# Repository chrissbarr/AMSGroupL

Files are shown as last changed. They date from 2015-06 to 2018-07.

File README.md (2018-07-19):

# Aim
The aim of our project is to design a robot that will demonstrate capabilities useful for search and rescue and emergency response operations. Our intended design will be capable of navigating and mapping a largely unknown environment, detecting and localising sound-emitting objects or persons, and determining a person’s status based on observed body temperature, detected sounds (as of breathing, talking, cries for help) and any observed motion using the on-board camera.

This capability could then be used either to notify on-site responders to the presence and locations of potential rescue candidates, or possibly even to provide some form of immediate assistance or medical treatment – however, that is outside of the bounds of this project, and is simply an example of the real-world applications of the system. For the purposes of this project, the system will sound an audible alert if a potential survivor is detected.

# Required Hardware
Our system will use a LIDAR unit for localisation and environmental mapping (SLAM), an IR temperature sensor to measure object temperatures in order to differentiate between debris and living people, and an array of microphones in order to perform sound localization. 

# Needs
* Ability to simultaneously localise within and map a bounded, but largely unknown environment
* Ability to navigate the environment based on the internally generated map
*	Ability to locate potential survivors based on sound
*	Ability to determine if a potential survivor is living or not
*	Ability to alert others to presence of survivor

# Requirements
## Core Requirements
*	Able to map the immediate environment as an occupancy grid that correlates with 85% to the ideal occupancy grid.
*	Able to accurately measure temperature of nearby objects (< 50cm, in front of IR temp sensor) within +/- 2°C.
*	Able to choose the most efficient pathway through the mapped environment > 90% of the time.
*	Able to localise multiple impulse sound sources within a 10m radius to within +/- 50cm accuracy, in robot-centric coordinates (as in finding preplaced sonic beacons). In a multi-robot scenario, such beacons will notionally have been placed by a previous "pathfinder" robot, which we will simulate by manual placement of beacons.
*	Able to traverse the perimeter of a detected object (e.g. Lumelski-class algorithms) while maintaining a fixed distance from the perimeter within +/- 5%.
*	Able to determine (with 75% accuracy) whether or not the object of interest is a living person.

## Extension Requirements
*	Able to successfully image the object of interest with 75% certainty that the correct object is the subject.
*	Able to detect the motion of nearby objects in front of the platform (for objects > 10cm moving at > 0.1 m/s). This is simply detecting whether or not there is motion, not the properties of that motion.
*	Capable of selecting station points around an object of interest (ranging from the size of the robot to the size of a prone person) for the purposes of achieving efficient imaging coverage (with overlap between successive images of 10% +/- TBD) at a distance from the object dependent on the given cameras FOV.

# Test Method
The proposed system will be required to navigate a test space consisting of unknown stationary obstacles, sporadic-sound sources both at temperatures in the defined human body-temperature range (simulated by an actual person), and at other temperatures outside this range (simulated by a radio or similar sound emitting object). 

The system will be evaluated on how accurately it can localise a sound source, how successfully it can navigate the unknown environment towards that sound source, and how effective its ability to differentiate between survivor candidates and other sound sources.

# Group Members
*	Chris Barr
    * SLAM
    * IR Temp
*	Bobby Nansel
    *	Sound Detection and Localisation
*	Eric Lai
    *	Close-Range Object Avoidance
    *	Dead Reckoning (Motor Encoders + IMU)
*	Premkumar Katti
    *	Navigation
    *	Path Planning

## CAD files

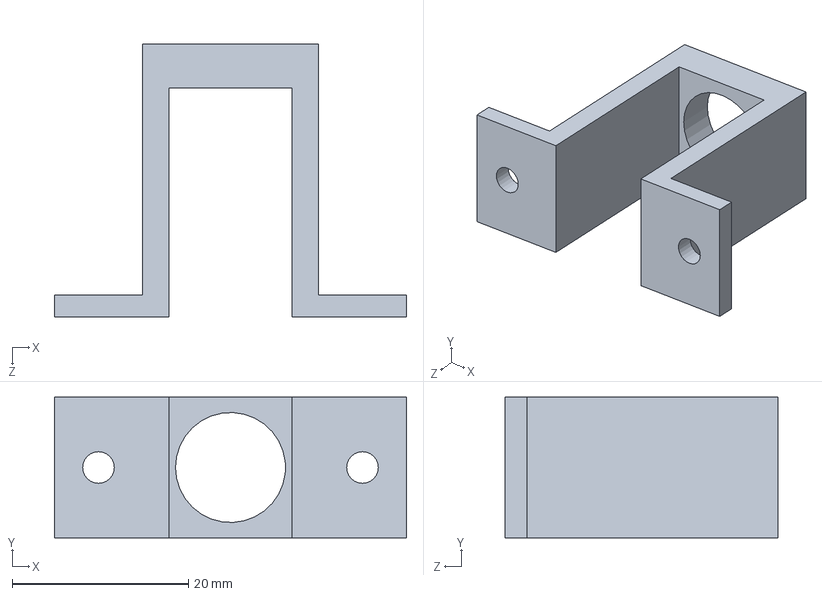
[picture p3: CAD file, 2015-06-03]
IRTempBracket/bracket1.SLDPRT
40.0 x 16.0 x 31.0 mm

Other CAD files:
IRTempBracket/bracket1_2.STL
IRTempBracket/bracket1.STL

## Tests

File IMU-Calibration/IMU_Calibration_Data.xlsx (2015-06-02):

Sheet: Calibration
Accelerometer Calibration |  |  |  | Gyroscope Calibration |  | Magnetometer Calibration
Orientation | X | Y | Z | Noise Upper Limit | 18 |  | X | Y | Z
0 | -0.12 | -5.73 | 238.91 | Minimum Angular Velocity | 40.00 | Min | -527.37 | -705.77 | -552.12
1 | 0.00 | -3.67 | -283.95 | Yaw (Table Edge) | 0.00 | Max | 547.05 | 503.17 | 472.97
2 | -46.75 | -268.88 | -25.88 | Yaw (1/2 rotation) | 179000.00
3 | 45.79 | 259.43 | -22.79 | Difference: | 179000 | Scale | 537.21 | 604.47 | 512.55
4 | -263.80 | 41.00 | -25.80 | Gyro Scale | -56977.46963 | Offset | 9.84 | -101.30 | -39.58
5 | 262.50 | -52.12 | -21.75
Scale: | 263.15 | 264.15 | 261.43
Offset: | -0.65 | -4.72 | -22.52

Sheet: 0
0 | -6 | 239
0 | -6 | 238
0 | -6 | 239
0 | -6 | 239
-1 | -5 | 239
0 | -5 | 239
0 | -5 | 239
0 | -6 | 239
0 | -6 | 239
0 | -5 | 239
0 | -6 | 239
0 | -6 | 239
0 | -6 | 239
0 | -5 | 239
0 | -5 | 239
0 | -6 | 239
0 | -6 | 239
-1 | -6 | 239
0 | -6 | 239
0 | -6 | 239
0 | -6 | 239
0 | -6 | 239
-1 | -5 | 238
0 | -6 | 239
0 | -6 | 238
0 | -6 | 239
0 | -6 | 239
-1 | -6 | 239
0 | -6 | 239
0 | -6 | 239
0 | -5 | 239
0 | -6 | 239
0 | -5 | 239
-0.1212121212 | -5.727272727 | 238.9090909
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

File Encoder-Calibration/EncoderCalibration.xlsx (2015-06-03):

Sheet: Calculations
 |  |  |  |  |  | Encoder Data
 | Vicon Reference Data (m) |  |  |  |  | Left Encoder |  |  | Right Encoder |  |  | Average
 | Start X | Start Y | End X | End Y | Distance Travelled | Start | End | Difference | Start | End | Difference |  | mm / tick
Trial 1 | 3.38 | 2.55 | 4.57 | 2.48 | 1.19 | 50251 | 75407 | 25156 | 50293 | 75496 | 25203 | 25179.5 | 0.0474
Trial 2 | 5.75 | 2.43 | 6.94 | 2.40 | 1.18 | 100464 | 125510 | 25046 | 100606 | 125701 | 25095 | 25070.5 | 0.0472
Trial 3 | 6.89 | 2.33 | 5.70 | 2.44 | 1.19 | 125509 | 150677 | 25168 | 125701 | 150905 | 25204 | 25186 | 0.0472
Trial 4 | 5.70 | 2.44 | 4.51 | 2.55 | 1.19 | 150677 | 175840 | 25163 | 150905 | 176109 | 25204 | 25183.5 | 0.0474
Average |  |  |  |  | 1.19 |  |  | 25133.25 |  |  | 25176.5 | 25154.875 | 0.0473
Angular: | Actual | Calculated | Diff | %
 | 18.24955592 | 18.80355592 | 0.554 | 97.05374876%
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

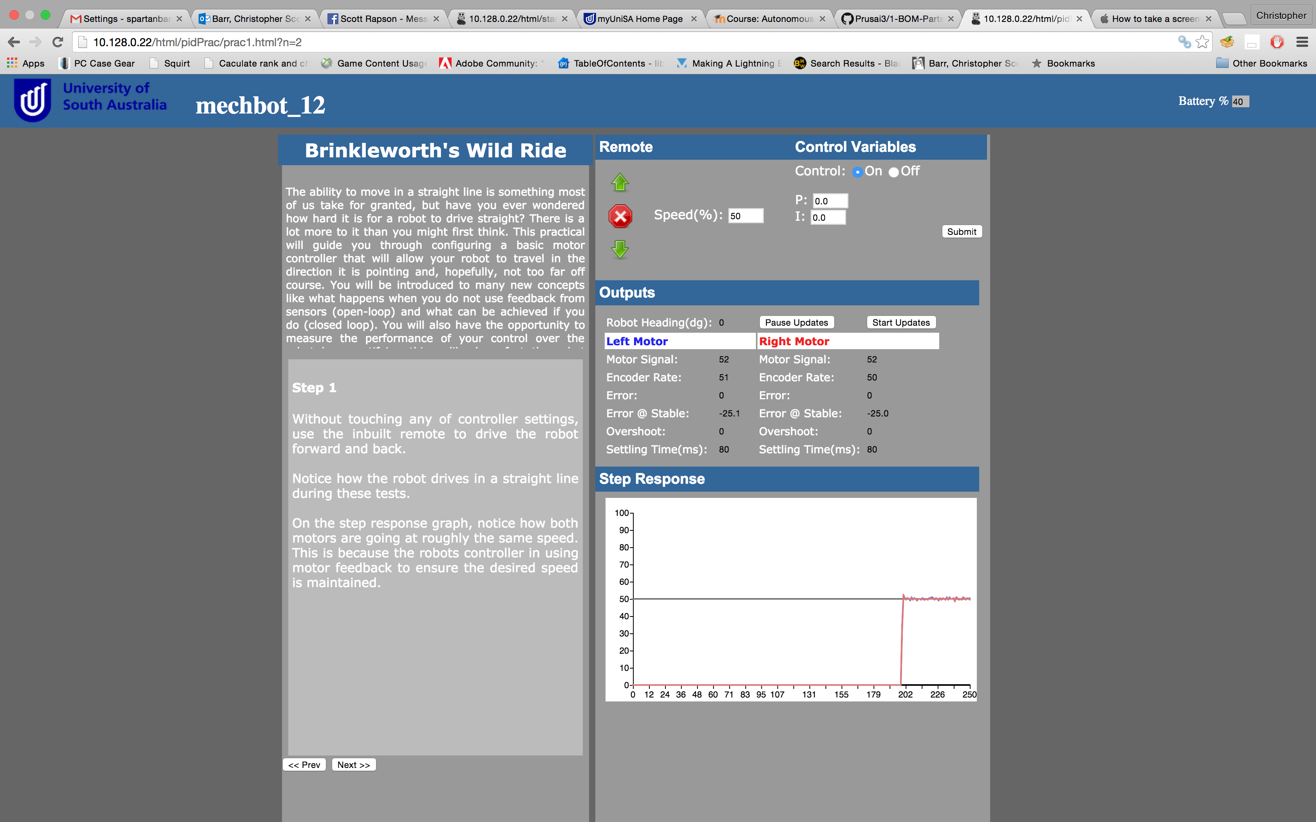
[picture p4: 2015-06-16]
Testing/MotorControlTesting/50percentLOAD.png

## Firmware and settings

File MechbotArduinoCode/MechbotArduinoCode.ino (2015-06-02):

//////////////////////////////////////////////////////////////////////////////////////////
//
//  Copyright (c) 2013 - 2015, University of South Australia
//  All rights reserved.
//
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
//////////////////////////////////////////////////////////////////////////////////////////
//
//  File            :  mechbot_v3_1_student.ino
//
//  Project         :  MechBot UGV Platform
//
//  Author(s)       :  Russell Brinkworth
//
//  Contributor(s)  :  Joseph East, Graeme Robertson, Darren Veenstra, Colin Smith,
//                     Daniel Griffiths & Phil Skelton
//
//  Maintainer(s)   :  Russell Brinkworth, Daniel Griffiths & Phil Skelton
//
//  Creation Date   :  24th January, 2013
//
//  Latest Update   :  19th February, 2015
//
//////////////////////////////////////////////////////////////////////////////////////////
//
//  Description: Arduino code to run the MechBot UGV platforms.
//
//  Note the following order of declaration:
//
//    1. Libraries.
//    2. Device hooks, ROS messages, global variables.
//    3. Function prototypes.
//    4. Publishers.
//    5. Subscriber callbacks.
//    6. Subscribers.
//    7. Arduino structures.
//    8. Your functions.
//    9. Helper functions.
//
//  Tested with LUbuntu 14.04 and ROS Indigo (Phil Skelton, December 2014).
//  Absolutely no guarantees are provided for compatibility with other versions.
//
////////////////////////////////////////////////////////////////////////////////////////////
//
//  Version history:
//
//    1.0.0 : Initial version.
//    1.1.0 : Increased analog inputs.
//    2.0.0 : Reordered code.
//            Optimised loops.
//            Added loop timers.
//            Staggered sensor updates.
//    2.1.0 : Changed ultrasonics from blocking call to interrupt to reduce loop time.
//    2.1.1 : Removed some orphaned function definitions.
//    2.1.2 : Replaced constants with defines.
//    2.2.0 : Integrated IMU into code.
//    2.3.0 : Reworked loop timing so code runs faster.
//            Control system on-off with variable.
//            Delay to ultrasonic first ping.
//            Gyro drift removal for z-axis.
//    2.3.1 : Resorted code order in main loop.
//            Battery capacity based on minimum cell voltage.
//            Encoder counts estimate lost ones due to missing interrupts and correct for loop time.
//            Ultrasonic power turned on during initialisation.
//    2.3.2 : Reordered code in main loop, now with 25Hz updates on most ROS communications.
//            Relabelled ultrasonics.
//    2.3.3 : Reduced speed of updates in main loop to be 10Hz communication through ROS rather than 25Hz.
//    2.3.4 : Removed function prototypes. REVOKED IN VERSION 3.1.0 (Phil Skelton)
//            Tidied up variable names.
//            Enacted 'Request IP' message over ROS as LCD_status.
//            Tidied up formatting.
//            Remove servo status topic.
//    2.3.5 : Filter for IR sensors and separated reading from publishing.
//    2.3.6 : Motor controller variables modified over ROS.
//    2.3.7 : Optional high speed encoder values.
//    3.0.0 : Rewrite for version 2 of the hardware.
//    3.1.0 : Updated code for version 3 of hardware (primary CPU upgrade).
//            Re-formatted, spell-checked, tidied up (to a limit) the entire code.
//            Changed all non-library variables, definitions and functions from 'camelCase' to 'underscores' formatting.
//            Forced ROS topics to use a constant prefix that should be unique to each robot (e.g. mechbot_01, bivbot_01).
//            Revoked a change implemented in version 2.3.4 and reimplemented function prototypes.
//            Cleared LCD incomming message when battery % written.
//    3.1.0s: Student version. Filters and control code removed.
//            Accurate loop timing removed.
//            Battery capacity model and display checks removed.
//            Check for multiple LCD messages removed.
//            Removed high speed encoder option.
//            Put all subroutines into a single main loop.
//
//////////////////////////////////////////////////////////////////////////////////////////


//////////////////////////////////////////////////////////////////////////////////////////
// 1. Libraries.
//////////////////////////////////////////////////////////////////////////////////////////

#include <ros.h>
#include "std_msgs/Int32.h"
#include "std_msgs/Int32MultiArray.h"
#include "std_msgs/Float32.h"
#include "std_msgs/Float32MultiArray.h"
#include "std_msgs/String.h"
#include "std_msgs/UInt8.h"
#include "std_msgs/UInt8MultiArray.h"

#include <ADXL345.h> // Accelerometer library.
#include <Arduino.h>
#include <HMC58X3.h> // Magnetometer library.
#include <ITG3200.h> // Gyroscope library.
#include <LiquidCrystal.h>
#include <PinChangeInt.h> // Interrupt library that allows extra pins to be used.
#include <Servo.h>
#include <stdlib.h>
#include <Wire.h>

#include "IRTemp.h"


//////////////////////////////////////////////////////////////////////////////////////////
// 2. Device hooks, ROS messages, global variables.
//////////////////////////////////////////////////////////////////////////////////////////

ros::NodeHandle node_handle; // Mandatory ROS initialiser.

// Students needs to change this constant to be what their MechBot is.
// For all intents and purposes, this should match both the physical label on the robot, and the VICON label.
// All ROS messages will use this prefix.
const String ROBOT_IDENTIFIER = "/mechbot_12"; // CHANGE THIS NAME TO MATCH THE SYSTEM NAME!

// Students should not change these values.
const String GETTER_IDENTIFIER = "/get";
const String SETTER_IDENTIFIER = "/set";

boolean got_connection = false; // Flag to say if got connection, as defined by a message sent to LCD for display over ROS.

// ------------------------ Motor Speed Controller Variables ------------------------

const String MOTOR_CONTROL_TOPIC_STRING = ROBOT_IDENTIFIER + SETTER_IDENTIFIER + "/motor_control";
const char * MOTOR_CONTROL_TOPIC = MOTOR_CONTROL_TOPIC_STRING.c_str(); // ROS topic for motor control.

int motor_speed_left = 0; // Motor speed reference.
int motor_speed_right = 0;
float control_data[5] = {0.0, 0.0, 0.0, 0.0, 0.0}; // Motor control values (on?, Proportional, Integral, Derivative, Encoders High Speed).
// Put in motor controller variables here.
int error_sum[2] = {0, 0};
int error_prev[2] = {0, 0};

#define PID_HARDCODED //if defined, PID values will be locked to the below values:
#ifdef PID_HARDCODED
float p = 2;
float i = 0.5;
float d = 0.1;
#endif


// ------------------------ Battery values specific section ------------------------

// Battery monitoring setup
#define BMS_ADDRESS 0x0DA7 // I2C address for battery management system.
#define TC_CAPACITY 20.0 // Time constant for battery capacity readings.

enum // Possible commands to send to battery management system.
{
  MIN_CELL_VOLTAGE = 1, // Request minimum cell voltage.
  CELL_NUMBER, // How many cells are connected in battery (3 is expected, 6 is maximum).
  BATTERY_VOLTAGE, // Total voltage from battery.
  CELL_VOLTAGES, // Voltage of each cell.
  SYS_CURRENT, // Current being used by system.
  OPP_TEMP, // Operating temperature.
  EX_VOLTAGE, // External voltage value.
  SHUTDOWN, // Tell system to shutdown.
};

const String BATTERY_STATUS_TOPIC_STRING = ROBOT_IDENTIFIER + GETTER_IDENTIFIER + "/battery_status";
const char * BATTERY_STATUS_TOPIC = BATTERY_STATUS_TOPIC_STRING.c_str();

unsigned char BMS_msg[32] = {0}; // Buffer for battery management system signals.
int cell_voltage = 0; // Variable holding the minimum cell voltage from the battery management system.
float battery_data[2]; // Current set up for 2 battery values (battery capacity, current draw), can be changed.
float battery_level = 0; // Last displayed battery level.
// Can put variables for battery capacity filter and/or display timing here.
float battery_max_mv = 4000;
float battery_min_mv = 3150;
std_msgs::Float32MultiArray battery_msg; // ROS message variable for battery and power data.


// ------------------------ Force sensor specific section ------------------------

#define FORCE_PIN A5

const String FORCE_STATUS_TOPIC_STRING = ROBOT_IDENTIFIER + GETTER_IDENTIFIER + "/force_status";
const char * FORCE_STATUS_TOPIC = FORCE_STATUS_TOPIC_STRING.c_str();

float force_data[1]; // Current set up for 1 force value, can be changed.

std_msgs::Float32MultiArray force_msg;


// ------------------------ IMU specific section ------------------------

#define GYRO_LIMIT 20.0 // Constant for gyro movement limit before stop including value in drift correction calculation (i.e. adaptive filter).
#define GYRO_TC 100.0 // Time constant for gyro offset calculation (x, y, z).

ADXL345 Accel;//ADXL345 accel;
HMC58X3 magn;
ITG3200 gyro = ITG3200();

const String IMU_STATUS_TOPIC_STRING = ROBOT_IDENTIFIER + GETTER_IDENTIFIER + "/IMU_status";
const char * IMU_STATUS_TOPIC = IMU_STATUS_TOPIC_STRING.c_str();

float mag_offset[3] = {9.84, -101.30, -39.58}; // Magnetometer offset calibration values. These will be different for every IMU.
//float mag_scale[3] = {537.21, 604.47, -512.55}; // Magnetometer scale calibration. These will be different for every IMU.
float mag_scale[3] = {537.21, 604.47, -512.55}; // Magnetometer scale calibration. These will be different for every IMU.

float IMU_data[9]; // Setup array for IMU data. 3 x acceleration, 3 x magnetometer and 3 x gyroscope.
int acc_data[3]; // Accelerometer needs a vector to put data into.
float acc_offset[3] = {0, 0, 0}; // Accelerometer offsets.
float acc_scale[3] = {263.15, 240.00, 261.43}; // Accelerometer gains.

float gyro_data[3]; // Gyro needs a vector to put data into.
float gyro_offset[3] = {0, 0, 0}; // Nominal gyro offset values for all 3 axes to remove drift. Must be very close to real value to start with but will be updated by the adaptive filter.
float gyro_scale = -56977.47; // Gyroscope scale value. Convert to radians / second.

std_msgs::Float32MultiArray IMU_msg; // ROS message variable for IMU data.


// ------------------------ InfraRed sensor specific section ------------------------

// Put time constant for IR LPF here.

const String IR_STATUS_TOPIC_STRING = ROBOT_IDENTIFIER + GETTER_IDENTIFIER + "/IR_status";
const char * IR_STATUS_TOPIC = IR_STATUS_TOPIC_STRING.c_str();

const unsigned int IR_SENSOR_PINS[4] = {A1, A2, A3, A4}; // Set the signal pins for the IRs (rear, right, left, front).
const unsigned int IR_ENABLE_PINS[4] = {53, 49, 48, 47}; // Set the enable pins for the IRs.

float IR_data[4]; // Current set up for 4 IR sensors, can be changed.
// Put variable for previous values for IR LPF here.

std_msgs::Float32MultiArray IR_msg;


// ------------------------ LCD specific section ------------------------

//#define LCD_RW 39 // R/W pin for LCD
#define LCD_NUM_CHARS 16 // Number of characters in a line on the LCD.

LiquidCrystal charLCD(40, 39, 38, 33, 32, 31, 30); // Setup for the default, set your own pins if necessary (RS, RW, EN, D4, D5, D6, D7).

const String LCD_WRITE_TOPIC_STRING = ROBOT_IDENTIFIER + SETTER_IDENTIFIER + "/LCD_write";
const char * LCD_WRITE_TOPIC = LCD_WRITE_TOPIC_STRING.c_str();
const String LCD_STATUS_TOPIC_STRING = ROBOT_IDENTIFIER + GETTER_IDENTIFIER + "/LCD_status";
const char * LCD_STATUS_TOPIC = LCD_STATUS_TOPIC_STRING.c_str();

boolean LCD_new_message = true;
boolean refresh_screen = false; // Boolean to make LCD writes go on alternate lines.
char LCD_incoming_msg[LCD_NUM_CHARS + 1]; // This is where the LCD message is stored once it has been received from ROS. Need one extra character for the terminating null character.

std_msgs::String LCD_msg; // Holds string last printed to the LCD.


// ------------------------ IP address specific section ------------------------

const String IP_ADDRESS_TOPIC_STRING = ROBOT_IDENTIFIER + GETTER_IDENTIFIER + "/IP_address";
const char * IP_ADDRESS_TOPIC = IP_ADDRESS_TOPIC_STRING.c_str();

char IP_address_msg[LCD_NUM_CHARS + 1];

boolean new_IP_address = true;


// ------------------------ Motor specific section ------------------------

#define MOTOR_ADDRESS 0x0DB7 // I2C address for motor controller.
#define MOTOR_MAX 4000 // Maximum value to send to motors.

enum // Possible commands to send to motor controller.
{
  PWM_left = 1, // Speed of left motor (0 to 4000).
  PWM_right, // Pulse width to right motor (0 to 4000).
  enc_left_and_right, // Encoder values of left and right motor (16-bit left, 16-bit-right).
  motor_temp, // Current operating temperature.
  motor_current, // System current usage (* 5 / 1024 to convert to Amp).
  flag_motor_direction, // Motor direction (0 = forward, 1 = reverse, 2 = clock-wise, 3 = counter-clock-wise).
  enc_time, // Time since encoders last read (* 32 to convert to us).
  enc_overflow, // Did encoder timing overflow (0 = no, 255 = yes).
  motor_enable // Enable motors (0 = no, 255 = yes).
};
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
void loop() // Main system loop. Everything runs from here.
{
  node_handle.spinOnce(); // Start-up code. Only do on first run. Starts ROS communication callbacks.

  if (!got_connection) // Keep requesting IP if no response received on ROS message LCD command.
  {
    LCD_msg.data = "REQUEST IP"; // Ask system for IP address to be displayed on LCD.
    LCD_publisher.publish(&LCD_msg); // Publish the IP request over ROS as LCD message. No need to keep displaying it on the LCD.
  }

  // Functions that need to be published every loop go here.
  IR_get(); // Get and filter IR values.
  loop_timing(); // Ensures accurate loop timing between calls to this function.
  drive(); // Determine values to send to the main drive motors.
  time_message(); // Publish Arduino code timing value(s). Is it needed every loop?
  
  // Functions that do not need to be published every loop go in one of these cases.
  if (loop_number == 0)
  {
    IMU_message(); // Get IMU values and publish on ROS.
    IR_temp_get();
    IR_temp_publish();
  }
  else if (loop_number == 1)
  {
    encoder_message(); // Only publish here if need low speed updates. If high speed needed then put outside of case statement.
    motor_publish(); // Only publish motor values to ROS here. 
  }
  else if (loop_number == 2)
  {
    battery_message(); // Get and publish battery / power values to ROS.
    //battery_display(); // How often do you want to print this to the LCD?
    force_message(); // Get analog value from force sensor and publish on ROS.
    IR_message(); // Only publish IR values to ROS here.
  }
  else if (loop_number == 3)
  {
    if (millis() > US_WAIT || US_on) // Only run ultrasonics after a start up delay. Would turn ultrasonics off when time function resets every 70 minutes so also use flag to say when ultrasonics have started.
    {
      US_on = true; // Flag ultrasonics as having started so they are not paused if timing value resets.
      US_message(); // Publish US data, if there is any new data.
    }
  }
  
  if (loop_number == 4) // See if system is on the last loop.
  {
    loop_number = 0; // Reset the loop counter.
  }
  else
  {
    loop_number++; // Increment the loop counter.
  }
}


//////////////////////////////////////////////////////////////////////////////////////////
// 8. Your functions.
//////////////////////////////////////////////////////////////////////////////////////////

void battery_message() // Need to convert raw values into useful units.
{
  // Find battery capacity remaining.
  send_command(BMS_ADDRESS, MIN_CELL_VOLTAGE, 0); // Request minimum cell voltage.
  delay(1); // Wait for battery management system to respond.
  send_request(BMS_ADDRESS, BMS_msg, 2); // Get minimum cell voltage from the battery management system.
  battery_data[0] = get_bytes_from_n(BMS_msg, 1); // Get signal from battery management system and put in battery data for transmission over ROS.

  // Put model for converting PWM signal from battery management system into battery capacity here.
  battery_data[0] = map(battery_data[0],battery_min_mv,battery_max_mv,0,100);
  // Find current usage
  send_command(BMS_ADDRESS, SYS_CURRENT, 0); // Request current usage.
  delay(1); // Wait for battery management system to respond.
  send_request(BMS_ADDRESS, BMS_msg, 2); // Get current usage from the battery management system.
  battery_data[1] = get_bytes_from_n(BMS_msg, 1); // Convert for transmission. Need to convert to mA.

  //battery_data[0] = round(battery_data[0]); // Round for transmission over ROS. This is needed if formula and filtering are used to convert the values.
  //battery_data[1] = round(battery_data[1]); // Round for transmission over ROS.
  battery_msg.data_length = 2;
  battery_msg.data = battery_data;
  battery_publisher.publish(&battery_msg); // Publish battery values on ROS network.
}

void loop_timing()
{
  while(micros() - last_loop_micros < LOOP_DELAY - 10)
  {
    delayMicroseconds(20); // This loop timing is inaccurate and does not take processing time into account. A better timing function is required.
  }
  last_loop_micros = micros();
}

void drive()
{
  get_encoders(); // Get the encoder values from the motor controller.
  // May need to scale velocity of wheels by actual time taken.
  
  #ifdef PID_HARDCODED
  control_data[0]=1;
  #endif
  
  if (control_data[0] == 1) // Left motor.
  {
    // Left motor speed control goes here.
    // Without code here the motor will not turn if the controller is turned on.
    motor_speed_left = pid_motor_control(0);
    /*
    int error = motor_left * 2 - abs(encoder_data[0]);
    motor_speed_left = 16 * (error * 1);
    */
  }
  else
  {
    motor_speed_left = 16 * motor_left; // No control system code. Just pass value out to motors with gain to scale up output from 8- to 12-bits.
  }

  if (motor_speed_left < 0 || motor_left <= 0) // These conditions set the speed within allowable range.
  {
    motor_speed_left = 0;
    error_sum[0] = 0;
    // TIP: reset intergral error to 0 here in order to reduce intergrator windup.
  }
  else if (motor_speed_left > 4000 || motor_left >= 255) // Make sure not to exceed allowable maximum speed.
  {
    motor_speed_left = 4000;
  }
  else
  {
    // Let the value pass.
  }

  if (control_data[0] == 1) // Right motor.
  {
    motor_speed_right = pid_motor_control(1);
    // Right motor speed control goes here.
    // Without code here the motor will not turn if the controller is turned on.
  }
  else
  {
    motor_speed_right = 16 * motor_right; // No control system code. Just pass value out to motors with gain to scale up output from 8-bits to 12-bits
  }

  if (motor_speed_right < 0 || motor_right <= 0) // These conditions set the speed within allowable range.
  {
    motor_speed_right = 0;
    error_sum[1] = 0;
    // TIP: reset intergral error to 0 here in order to reduce intergrator windup.
  }
  else if (motor_speed_right > 4000 || motor_right >= 255) // Make sure not to exceed allowable maximum speed.
  {
    motor_speed_right = 4000;
  }
  else
  {
    // Let the value pass.
  }

  // Send updated motor speed values to motors, keeping existing direction.
  set_motors(motor_direction, motor_speed_left, motor_speed_right); // Need to cast motorSpeed as controller may force them to be floats.
}

int pid_motor_control(int motor_num) {
  int motor_output, error;
  float kp, ki, kd;
  uint8_t motor_setpoint;
  
  
  kp = control_data[1];  //proportional multiplier
  ki = control_data[2];  //integral multiplier
  kd = control_data[3];  //derivative multiplier
  
  //if we've hardcoded values in, use those instead
  #ifdef PID_HARDCODED
  kp = p;
  ki = i;
  kd = d;
  #endif
  
  //first, get the setpoint for the desired motor
  if(motor_num == 0) {
    motor_setpoint = motor_left;
  } else {
    motor_setpoint = motor_right;
  }
  
  //now, calculate the error between the setpoint and the current speed
  error = motor_setpoint - abs(encoder_data[motor_num]);
  
  error_sum[motor_num] += error;
  
  //next, calculate the desired speed for the motor
  motor_output = 16 * ((error * kp) + (error_sum[motor_num] * ki) + ((error - error_prev[motor_num]) * kd));
  
  error_prev[motor_num] = error;
  
  return motor_output;
  
}


void encoder_message() // Publish encoder data on ROS. Must run after drive.
{
  encoder_msg.data_length = 4;
  encoder_msg.data = encoder_data;
  encoder_publisher.publish(&encoder_msg);
}


void force_message() // Need to convert raw values into useful units.
{
  force_data[0] = analogRead(FORCE_PIN); // Gripper force sensor. Experiment to convert to useful units.
  force_msg.data_length = 1;
  force_msg.data = force_data;
  force_publisher.publish(&force_msg); // Publish force values on ROS network.
}


void IMU_message() // Send IMU values over network.
{
  Accel.readAccel(acc_data); // Get accelerometer data.
  // Calculate normalisation factor.
  for (int i = 0; i <= 2; i++)
  {
    IMU_data[i] = acc_data[i] / acc_scale[i] + acc_offset[i]; // Normalise accelerometer data and put into IMU vector.
  }

  magn.getValues(&IMU_data[3], &IMU_data[4], &IMU_data[5]); // Get magnetometer values.
  for (int i = 0; i <= 2; i++)
  {
    IMU_data[i + 3] = (IMU_data[i + 3] - mag_offset[i]) / mag_scale[i]; // Remove magnetometer offsets and apply scale.
  }

  gyro.readGyro(gyro_data); // Get gyro data.
  for (int i = 0; i <= 2; i++)
  {
    // Put drift calculation for gyro here.
    IMU_data[i + 6] = LOOP_DELAY * (gyro_data[i] - gyro_offset[i]) / (1000 * gyro_scale); // Put gyro data into IMU vector with drift removed. Scale data to rad.
  }

  IMU_msg.data_length = 9;
  IMU_msg.data = IMU_data;
  IMU_publisher.publish(&IMU_msg); // Publish IMU values on ROS network.
}
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

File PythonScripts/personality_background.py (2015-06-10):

#!/usr/bin/env python

"""
This program runs in the background, and is intended to add more personality to the mechbot.

It is designed to audibly react to certain events, including:
	- Being picked up / lifted
	- Being forcibly pushed along the ground
	- Being left alone for extended periods of time

"""

# system libraries
import time
import select
import sys
import socket
import os
import math
import pygame
from os.path import expanduser

import random
from random import randint
import numpy as np

# ROS libraries
import rospy
import std_msgs.msg
from geometry_msgs.msg import Point, Quaternion, PoseStamped, Pose
import tf

# My Modules
from OurModules import functions_personality as pf
from OurModules import functions_servo_control as servo

# IMU
acc_x = -999
acc_y = -999
acc_z = -999

# Encoder
encoder_left = 0
encoder_right = 0

# PERSONALITY CORE SETTINGS
talkativity = 1.0
pickup_threshold = .3	# z-accel value needed to trigger 'pick-up' event
pickup_comment_time_threshold = 8	# minimum time between 'pick-up' remarks
pushed_comment_time_threshold = 4
handshake_comment_time_threshold = 4
last_pickup_comment_time = 0	# tracks time last comment was made
last_handshake_comment_time = 0
last_played_sound = 'none'
last_action_time = time.time()
lonely_threshold_time = 120
motors_last_active_time = 0

# MOTOR SPEED VARIABLES
# Only used to check current motor speed
motor_direction = 0
motor_speed_left = 0
motor_speed_right = 0

## Gripper Force Variable
gripper_force = 0

delay = 0.1 # update rate for main loop (s)

rospy.init_node("personality_controller", anonymous=False) # name the script on the ROS network

def msg_subscriber():
	# subscribe to ROS data updates
	#CP = rospy.Subscriber("currentPose", PoseStamped, current_pose_update)
	EN = rospy.Subscriber("/mechbot_12/get/encoder_status", std_msgs.msg.Int32MultiArray,encoder_status_update)
	IMU = rospy.Subscriber("/mechbot_12/get/IMU_status", std_msgs.msg.Float32MultiArray,imu_status_update)
	MD = rospy.Subscriber("/mechbot_12/set/motor_drive", std_msgs.msg.Int32MultiArray, motor_drive_update)
	GR = rospy.Subscriber("/mechbot_12/get/force_status", std_msgs.msg.Float32MultiArray, force_status_update)
	return (IMU, MD, EN)

def imu_status_update(data):
	global acc_x, acc_y, acc_z
	acc_x = data.data[0]
	acc_y = data.data[1]
	acc_z = data.data[2]
	#print("IMU")
	
def motor_drive_update(data):
	global last_action_time, motor_direction, motor_speed_left, motor_speed_right, motors_last_active_time

	#print("motor drive update")

	motor_direction = data.data[0]
	motor_speed_left = data.data[1]
	motor_speed_right = data.data[2]
	if(motor_speed_left != 0 or motor_speed_right != 0):
		last_action_time = time.time()
		motors_last_active_time = time.time()
	#print("MOTORS")

def encoder_status_update(data):
	global last_action_time
	global encoder_left, encoder_right
	encoder_left = data.data[0]
	encoder_right = data.data[1]

	if(encoder_left != 0 or encoder_right != 0):
		last_action_time = time.time()
	#print("ENCODERS")

def force_status_update(data):
	global gripper_force
	gripper_force = data.data[0]
	#print("gripper update %f") % gripper_force

def loop_timing(delay,loop_start):
	loop_sleep = delay - (time.time() - loop_start) # if loop delay too low then will print data faster than updates are recieved
	if loop_sleep > 0:
		time.sleep(loop_sleep)

def check_motors_stopped():
	if(motor_speed_left == 0 and motor_speed_right == 0):
		return True
	else:
		return False

def check_encoders_stopped():
	if(encoder_left == 0 and encoder_right == 0):
		return True
	else:
		return False

def check_IMU_published():
	if(acc_x == -999 and acc_y == -999 and acc_z == -999):
		return False
	else:
		return True
		
def react_to_pickup():
	global last_pickup_comment_time, pickup_threshold, pickup_comment_time_threshold, last_action_time
	
	if(check_IMU_published()):
		# detect if picked up from IMU data - z liftoff means picked up any time, otherwise if motors are stopped but platform experiences any acceleration
		if(math.fabs(acc_z+1) > pickup_threshold):# or ((math.fabs(acc_x) > pickup_threshold or math.fabs(acc_y) > pickup_threshold) and (check_motors_stopped() and check_encoders_stopped()))):
			print("Put me down!")
			# robot is being handled / carried. Respond if appropriate:
			if(time.time() - last_pickup_comment_time > pickup_comment_time_threshold):
				# enough time has passed to make another remark...
				pf.play_sound_group(pf.sound_group_pickup,100)
				last_pickup_comment_time = time.time()
				last_action_time = time.time()

def react_to_pushed():
	global last_pickup_comment_time, pickup_threshold, pushed_comment_time_threshold, last_action_time, motors_last_active_time

	# if the wheels are moving but the motors are off, someone may be pushing the mechbot along
	if(check_motors_stopped() == True and check_encoders_stopped() == False):

		# wait a little bit, otherwise we'd detect the mechbot's stopping motions (motors told off but wheels still move for a moment)
		time.sleep(0.2)

		# check again - now we can be more certain if this is deliberate
		motor_time = time.time() - motors_last_active_time

		if(check_motors_stopped() == True and check_encoders_stopped() == False and motor_time > 2):
			print("Motor speeds: %d %d, Encoder Values: %d %d, Last motor time: %d") % ( motor_speed_left, motor_speed_right, encoder_left, encoder_right, motor_time)
			print("Quit pushing me around!")
			if(time.time() - last_pickup_comment_time > pushed_comment_time_threshold):
				# enough time has passed to make another remark...
				pf.play_sound_group(pf.sound_group_push,100)
				last_pickup_comment_time = time.time()
				last_action_time = time.time()
			
def react_to_lonely():
	global last_action_time, lonely_threshold_time
	if(time.time() - last_action_time > lonely_threshold_time):
		print("Getting lonely here...")
		pf.play_sound_group(pf.sound_group_lonely,30)
		last_action_time = time.time()

def react_to_gripper_squeeze():
	global last_handshake_comment_time, handshake_comment_time_threshold
	if(gripper_force > 200):
		if(time.time() - last_handshake_comment_time > handshake_comment_time_threshold):
			print("Handshake?")
			pf.play_sound_group(pf.sound_group_hello,100)
			last_action_time = time.time()
			last_handshake_comment_time = time.time()

def personality_core_init():
	random.seed()
	pf.sound_init()
	time.sleep(1)
	print("Hello! Personality Core initialised!")
	pf.play_sound_group(pf.sound_group_startup,100)
	pf.block_wait_sound_finish()
	servo.publish_servo(1000,550)	#move servo arm out of way for navigation / object avoidance

def personality_core_update():
	react_to_pickup()
	react_to_lonely()
	react_to_pushed()
	react_to_gripper_squeeze()
	
def personality_core_shutdown():
	pf.play_sound_group(pf.sound_group_shutdown,100)
	print ("Personality Core Disengaged. Shutting down...")

	pf.block_wait_sound_finish()

	pygame.mixer.quit()
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

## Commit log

2015-04-09 Added Arduino Code
    Uploaded Arduino code from today's practical. Loop timing is working
    well. Proportional control of left motor is working, awaiting
    abstraction to multi-motor setup and addition of integral and derivative
    control elements.
2015-04-12 PID Function
    Began to break PID motor control out into it's own function to allow
    application to both motors.
2015-04-14 PID Working
    PID controller is working (well, P + I, no D yet). Tested on mechbot.
2015-04-14 IR Temperature
    Draft code for IR Temperature measurement. Sensor library added, ROS
    publisher setup. Awaiting sensor to be wired up to test.
2015-04-26 Fixing Earlier Change
    Earlier motor_publish() function was changed to output different data for debug purposes. Reverting change.
    [MechbotArduinoCode.ino]
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2015-04-28 IR Bracket
    Added bracket design to fit IR temperature sensor
    [bracket1.SLDPRT, bracket1.STL]
2015-04-28 Update Bracket
    Updated IR bracket
    [bracket1.SLDPRT, bracket1.STL]
2015-04-30 New Python Scripts
    Worked on python scripts for IR, basic motor control. Added define to
    enable/disable IR sensor running when connected.
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2015-05-07 Odometry Works!
    Wheel odometry is matching Vicon data quite closely. Still need wheel
    calibration.
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2015-05-14 Hardcode PID Motor Driver
    Added in hardcoded values for PID motor controller. This is to save
    time manually setting the PID values before each test.
2015-05-14 Updated IRtoDistance
    Updated script to use different equations for each sensor, based on
    sensors measured output. Time checking also added.
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2015-05-14 Point to Point Working + IR Distance
    Most basic form working. Currently turns to face desired coordinate,
    then drives forward until it detects coordinate reached. No steering
    control implemented yet.
2015-05-14 Motor_Pilot2 Update
    Tidy up, break angle / coordinate calculations out into functions for
    code modularity / readability. Added in basic PI controller to try and
    keep robot heading towards target during straight-line moves. Requires
    testing.
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2015-05-15 Syntax Error
    Fixed error regarding battery mapping floats.
    [MechbotArduinoCode.ino]
2015-05-15 Changed min battery level
    Minimum battery level is now more in line with indicator on Mechbot.
2015-05-15 Motor Pilot
    Updated motor pilot to correctively steer towards target. Tested
    successfully, seems to be working well. Will adaptively steer based on
    proportional controller to keep target coordinate directly ahead. If
    error is too great, code stops, reorients robot and then resumes
    travel. Code is still messy, needs some tidying, leftover code from
    test-procedures / queued waypoints etc.
2015-05-15 Update minimum battery level
    Screen was reading as 30% charged when LED indicators were signalling battery depleted. Adjusting minimum battery level to more closely match. I should probably just measure the level of the battery 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
2015-05-15 Update motor_pilot2.py
    Changed coordinates_reached() to use the point-distance between the current and desired coordinates, rather than just checking a rectangular bounding box. Will be more accurate, slightly more computa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
2015-05-15 Update motor_pilot2.py
    Changed main loop rate to 10Hz. Was previously at 5Hz, however Vicon updates at 10Hz and wheel-encoder odometry will update at rate specified on Arduino (default 50Hz). Faster loop rate may smooth ou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
2015-05-19 dummy_grid_broadcaster.py
    Wrote basic program to broadcast a handmade dummy map with Prem’s help.
    Should be useful for pathfinding, was an exercise in figuring out how
    occupancy-grids are represented in ROS.
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2015-05-28 IMU Calibrated
    Calibrated IMU accelerometer, gyroscope and magnetometer according the
    advanced control systems practical sheet. Data has been collected and
    calibration values calculated, not yet applied to Arduino sketch.
    [IMU_Calibration_Data.xlsx]
2015-05-28 Bagged Data
    Bagged a bunch of data while the mechbot drove in a square pattern.
    Should be useful to compare odometry to Vicon data, especially in
    regards to turning accuracy.
    Need to do tuning on linear / angular elements of odometry still.
2015-05-29 IMU Calibration
    Added calibration values to main Arduino code
    [IMU_Calibration_Data.xlsx]
2015-05-29 Play Sound Script
    Added Russell’s updated script to play sounds on the Mechbot.
2015-05-29 Encoder Calibration
    Recorded Vicon / Encoder data while mechbot was moving in a straight
    line. Calculated move distance from Vicon data, used with Encoder data
    to calculate new ticks / mm value. New value is 10% different from old
    value - significant difference, hopefully new value is an improvement.
    [EncoderCalibration.xlsx, IMU_Calibration_Data.xlsx]
2015-05-30 Motor Controller Now PID
    Updated motor speed controller to PID (from PI). Untested, D is
    currently set to 0.1
2015-05-30 Example Script Work
    Continued work, sounds will no longer be played twice sequentially,
    many other improvements.
    [demo_script1.py]
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2015-05-30 Added IMU Heading Script
    Added Advanced Control systems IMU Heading python script. Will be
    needed to determine relative offset between IMU heading and Vicon
    system. Has useful mag / gyro sensor fusion example for determining
    heading.
2015-05-30 Object Avoidance
    Added script based on Eric’s object avoidance work. New script is
    designed to sit between higher-level scripts (point-to-point navigation
    etc) and the motors, will attempt to avoid obstacles and prevent
    collisions.
    [background_object_avoidance.py]
2015-06-02 Broke Out Shared Functions
    [background_personality.py, personality_functions.py]
2015-06-02 IMU Calibration
    [IMU_Calibration_Data.xlsx]
2015-06-02 Pathfinding Test
    Pathfinding working at basic level on robot. Work needed on motor_pilot
    script, rotations are not right.
2015-06-02 Object Avoidance Working
    Passthrough / background object avoidance is working at basic level.
    Had to swap motor messages over to Int32Multi from UInt8Multi.
    [MechbotArduinoCode.ino, background_object_avoidance.py, motor_pilot.py]
2015-06-02 Fixed Pickup Detection
    Math error
    [background_personality.py]
2015-06-03 Many Changes
    Restructured files / folders. Significantly reworked code. Preparing
    for demonstration.
    [bracket1.SLDPRT, bracket1_2.STL]
2015-06-03 Encoder Angular Calibration
    Calibrated wheel_base value in localisation script from experimental
    results.
    [EncoderCalibration.xlsx]
2015-06-04 Startup Scripts
    Added personality and object avoidance to start_ros_student.sh
    Volume on mechbot lowered to be more suitable.
    [personality_background.py]
2015-06-04 Personality Fix
    Fixed issue where lonely comments were not occurring. Motor / odometry
    updates were resetting counter. Changed so that they only effect
    counter if published values are non-zero.
    [personality_background.py]
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2015-06-04 Servo Control
    Servo control functions broken out. Personality script now raises arm
    on startup to assist object avoidance.
    [personality_background.py]
2015-06-04 Demo Script Bugfix
    Fixing problems.
    [demo_script1.py]
2015-06-04 Nav Bugfix
    Something somewhere is still wrong. Or maybe object avoidance is
    screwing with navigation more than I suspect.
    [nav_pilot.py]
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2015-06-04 Pathfinding Integration
    Swapping pathfinding script over to my modules.
    [path_dijkstra_search.py]
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2015-06-05 Updated Object Avoidance
    Improved response, turn-direction now depends on data from ultrasonic
    sensors - should usually cause mechbot to turn in direction that will
    work best. Sounds added.
    [object_avoidance_background.py, personality_background.py]
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2015-06-09 Nav, Loc update
    Significant update, fixed most point-to-point problems. Localisation
    fusion working intermittently, still need to find source of some errors.
    [demo_script1.py, loc_fusion.py, nav_pilot.py]
2015-06-09 Object Avoidance Overhaul
    Updated object avoidance based on practical tests. Mechbot will now
    attempt to steer away from obstacles alongside of it - however
    proportional feedback needs significant tuning.
    [object_avoidance_background.py]
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
